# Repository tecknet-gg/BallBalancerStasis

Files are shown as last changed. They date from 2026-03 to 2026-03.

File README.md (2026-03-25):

## Overview

A project where I make a cool 3RRS parallel manipulator, and throw a camera underneath and get it to balance a ball. It uses Computer Vision (CV) to locate the ball on the platform, and then the location and velocity vector will be used to calculate the pose of the platform (using Inverse Kinematics) to then push the ball back to the centre. 

I manily made this project since it seemed cool when I saw a couple of people who had made them on YouTube (https://www.youtube.com/watch?v=v4F-cGDGiEw&t=235s), and I (being masochistic), like using PID, so here we are!

The hardware for the most part is done, and the .step file can be found in the hardware folder. Firmware is still in the very early stages, and the balancing software is yet to be written.



With the custom PCB:



Here's the BOM:

| Component | Function | Quantity | Price (unit*qty) | Source |
| --- | --- | --- | --- | --- |
| Raspberry Pi Zero 2 W | Microcontroller | 1 | £14.15 | https://shop.pimoroni.com/products/raspberry-pi-zero-2-w?variant=42101934587987 |
| Pi Camera | Camera | 1 | £7 | https://www.amazon.co.uk/dp/B0BZVP3SQW |
| Pi Zero Accessories | Assorted Accessories | 1 | £8 | https://shop.pimoroni.com/products/zero-adaptor-kit?variant=10462230279 & https://shop.pimoroni.com/products/camera-cable-raspberry-pi-zero-edition?variant=32092803891283 |
| Tie Rod | Joint | 10 | £6.99 | https://www.amazon.co.uk/dp/B0DCNGSK9S/?coliid=IMXWIUSGWOUHA&colid=3NYE67N1E05KC&psc=1 |
| M3/M4 Assortment | Strcutural | ~ | £6.64 | https://amzn.eu/d/07FYMvyj |
| DS3218MG | Servos | 3 | £29.99 | https://www.amazon.co.uk/dp/B0CY2FVZZM/?coliid=I2RXC2YMY9KN9T&colid=3NYE67N1E05KC&th=1 |
| PCA9685 | Servo Driver | 1 | £4.99 | https://www.amazon.co.uk/dp/B0BKZC1XWR/?coliid=I37WT66U57CC7J&colid=3NYE67N1E05KC&psc=1 |
| Power Supply | Power | 1 | £16.99 | https://tinyurl.com/2cr9nb7n |
| Shoulder Bolts | Pin Joints | | £4.99 | https://www.amazon.co.uk/dp/B0FDQB24SP?ref=ppx_yo2ov_dt_b_fed_asin_title |
| PLA | Printing Material | 1 | £13.99 | https://www.amazon.co.uk/dp/B0CD79M1NV?ref=ppx_yo2ov_dt_b_fed_asin_title |
| 20mm Acrylic Disc | Platform Disc | 1 | £3.49 | https://www.amazon.co.uk/dp/B0DJVB82TY/?coliid=I2NBRJSN1CBSC1&colid=3NYE67N1E05KC&psc=1 |
| 18AWG Wire | Wire | 2 | £2.90 | https://www.amazon.co.uk/dp/B0CZRGH4CT/?coliid=I36BQ0C4MRSHG2&colid=3NYE67N1E05KC&psc=1 |
| PCB | PCB | 5 | £9 | JLCPCB |

## Assembly 

You'll want to print out the files under the hardware/compoents directory in the quantities given below:

| Component | Quantity |
| --- | --- |
| feet | 6 |
| standoffs | 6 |
| baseplate | 1 |
| shield | 1 |
| bottomarm | 3 |
| toparm | 3 |
| mount | 3 |
| mountclip | 3 |

With that we start with the base and the feet. For my build, I will add some hotglue to the bottom of the each feet (the side with the smaller radius), to act as a grip. With that, its just a matter of attaching them around the circumference of the base plate. Take care to not atttach them to the holes meant for the standoffs. Use M3x6 or M3x8 screws. They are part of the screw assortment kit in the BOM if you do decide to buy the same. Reference the image below to attach the feet to the correct points.

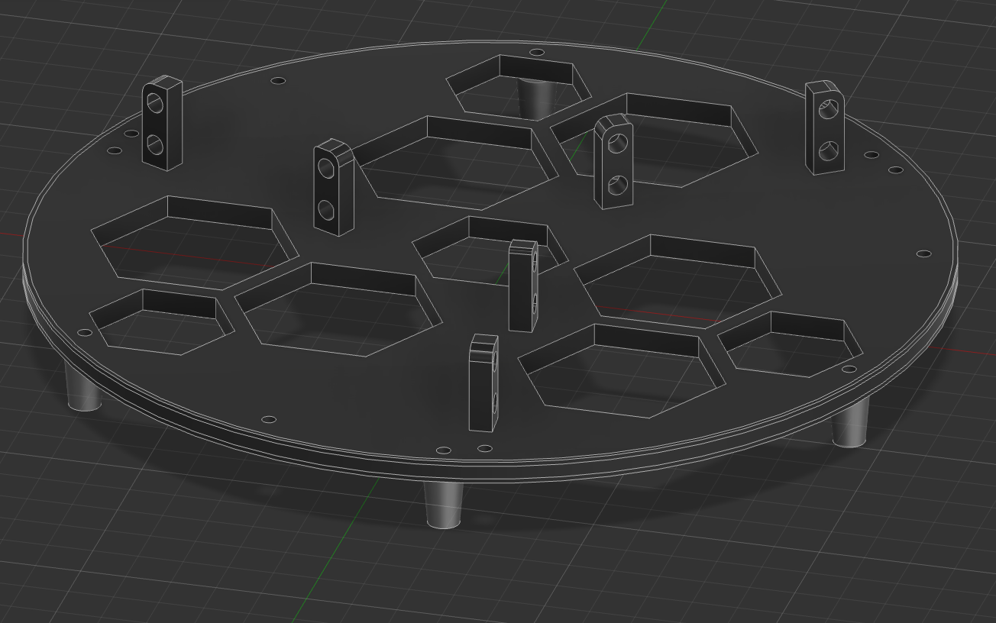
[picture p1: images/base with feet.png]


With the feet in, you'll want to grab your three servos and place them on the mounts as such:



Attach them using M3x10 bolt with a nut on the other end to clamp it in place. Also ensure you have attached the servo horn using the hardware given in the kit. Alternatively you can use an M3x6 bolt to attach the horn to the servo.

Then grab your six standoffs. Follow the same steps you did for the feet (except the hot glue grip), and attach them around the circumference using M3x8 bolts.



Now with your three bottom arms, line up the two holes on the bottom with the two on the servo horn. Using an M3x6 bolt, attach that too to the horn. You won't need a nut since the servo horn is threaded. 



Grab the three top arms now, and attach them to the bottom arms using the M4 shoulder bolt. If you want you can use a standard M4, but I use a tie rod for my build. Secure it on the other side using a lock-nut. Alternatively you could use two nuts twisted toghther tightly with some pliers.



Get your tie rods, and attach the to the top of each arm using an M3x6 or M3x8 Bolt.



You can now attach the electronics shield part to the standoffs. Just use the same M3x8 bolts and attach the shield to the six standoffs.



For the next part, my assembly doesn't have the correct compoenent in it since I don't want to redo it since I'm pretty sure I would screw up the joints, and I really don't want to do that again, so read carefully!

The mount you printed should look something like this:



You'll want to grab the M3x20mm bolt, and put it through one of the holes, then attach a nut. Proceed to screw the bolt in, and thread it through one of the tie rods. When it is on the other side of the tie rod, you'll want to add another nut. Then thread it through the other hole of the mount, and out the other end. At this side, you can use another lock nut to attach it securely. Repeat this for the three mounts. Ensure that the extended bit is pointing inwards and not outwards.

Ok now we can start assembling the electronics. Place the Pi Zero 2 W on the corresponding standoffs, and do the same with the PCA9685. No bolts required. Then place the camera module in its little enclosure. Use the attach the CSI cable to the camera, and the other end to the interface on the Pi Zero 2 (note: you'll probably need another cable specifically for the Pi Zero, one with a thinner end for the Pi Zero's CSI slot, as the stock cable with the camera is intended for the full size Pis). With the three main compoenents in, you can start wiring up the PCA9685 using this diagram (in the hardware directory):

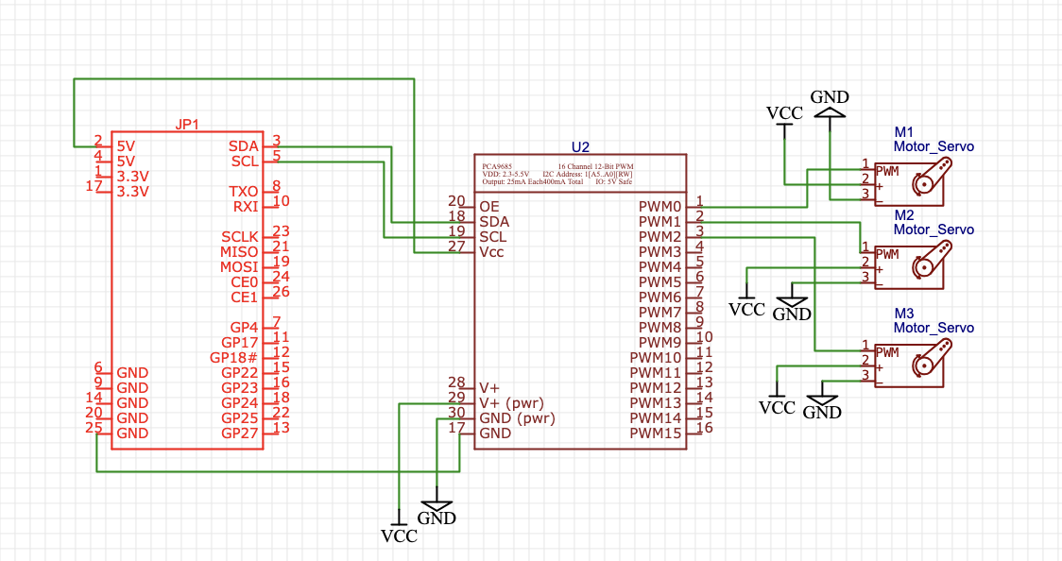
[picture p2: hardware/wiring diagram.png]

You can then attach the three servos to channels 0, 1 and 2 like in the diagram.

Finally for power, get a barrel jack to screw terminal mount, and just hot glue it somewhere onto the bottom. There's not really any mounting pounts on the screw terminal, so and I didn't really want to model in a recess specifically for that. Attach the two 18AWG wires to the screw terminals, and route it up to the PCA9685, and screw the wires into the corresponding screw terminals on the PCA9685. 

And now we can get onto mounting the platform. Grab your clear acrylic disc and the three mount clip parts. Its not on the 3D assembly, but you'll want first put some M3x6 screws through the main mount, then place the platoform in the recess, and get thread the mount clip onto the bolts, then tighten the screws. You shouldn't need a nut here, but if you end up using a longer bolt, you can. Though the piece is threaded so you shouldn't need to.



If you want to add the IMU mount like I will, you can print out the IMU Mount v4 file (x2), and just attach the IMU (MPU6050) to it, and attach it to the platoform as you did mounting the platform to the the top arm mount!



If you happen to be using the PCB, get yourself the board, solder on the DC Barrel Jack, the Pi Zero 2 W and the PCA9685. Then print out the PCB shield instead of the other shield, and mount the PCB on, and voila. Wire up the camera the same. You can wire the IMU into the I2C extender of the PCA9685 in both cases of using the PCB and not.

The PCB looks like so if you do decide to get it fabricated:



For assembling this, just desolder the headers from a Pi Zero 2 W, and put them on the underside, and solder that to the PCB. With the PCA9685, just desolder the headers too, and replace with vertical headers and again solder to the board, and you can place it on the corresponding shield! Also add 3mm LEDs if you so wish to :]

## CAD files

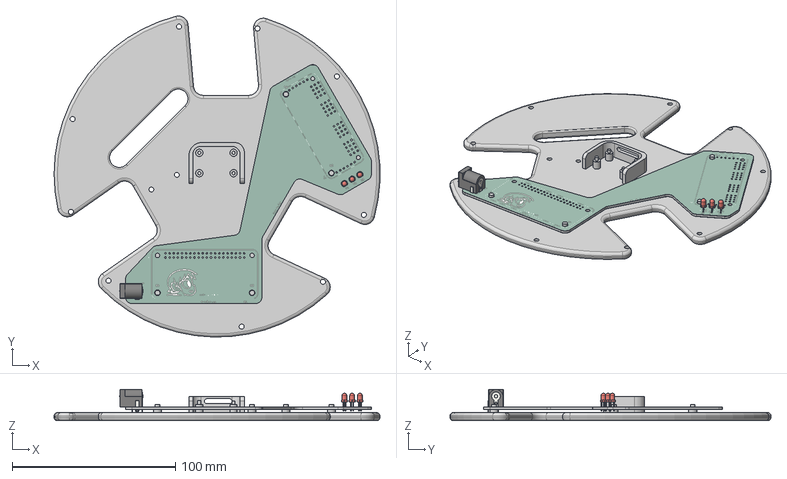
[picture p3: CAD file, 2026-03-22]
hardware/components/shieldpcb.step
199.9 x 196.9 x 19.3 mm
BarrelJack_Horizontal
LED_D3.0mm x 3
Ball Balancer_silkscreen
Ball Balancer_soldermask
Ball Balancer_PCB

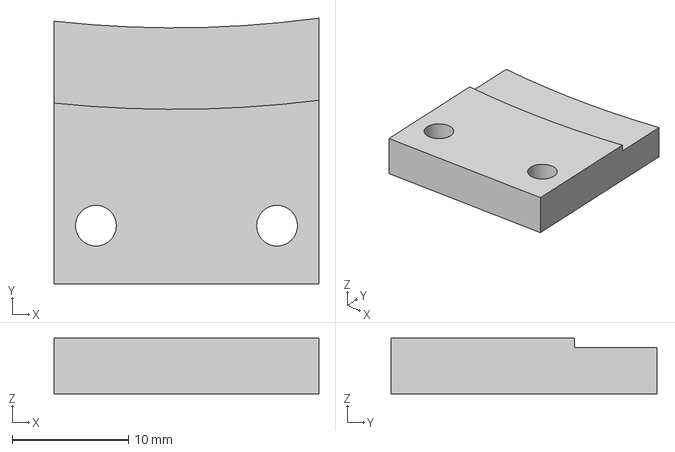
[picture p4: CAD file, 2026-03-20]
hardware/components/IMU mount v4.step
22.8 x 22.8 x 4.80 mm

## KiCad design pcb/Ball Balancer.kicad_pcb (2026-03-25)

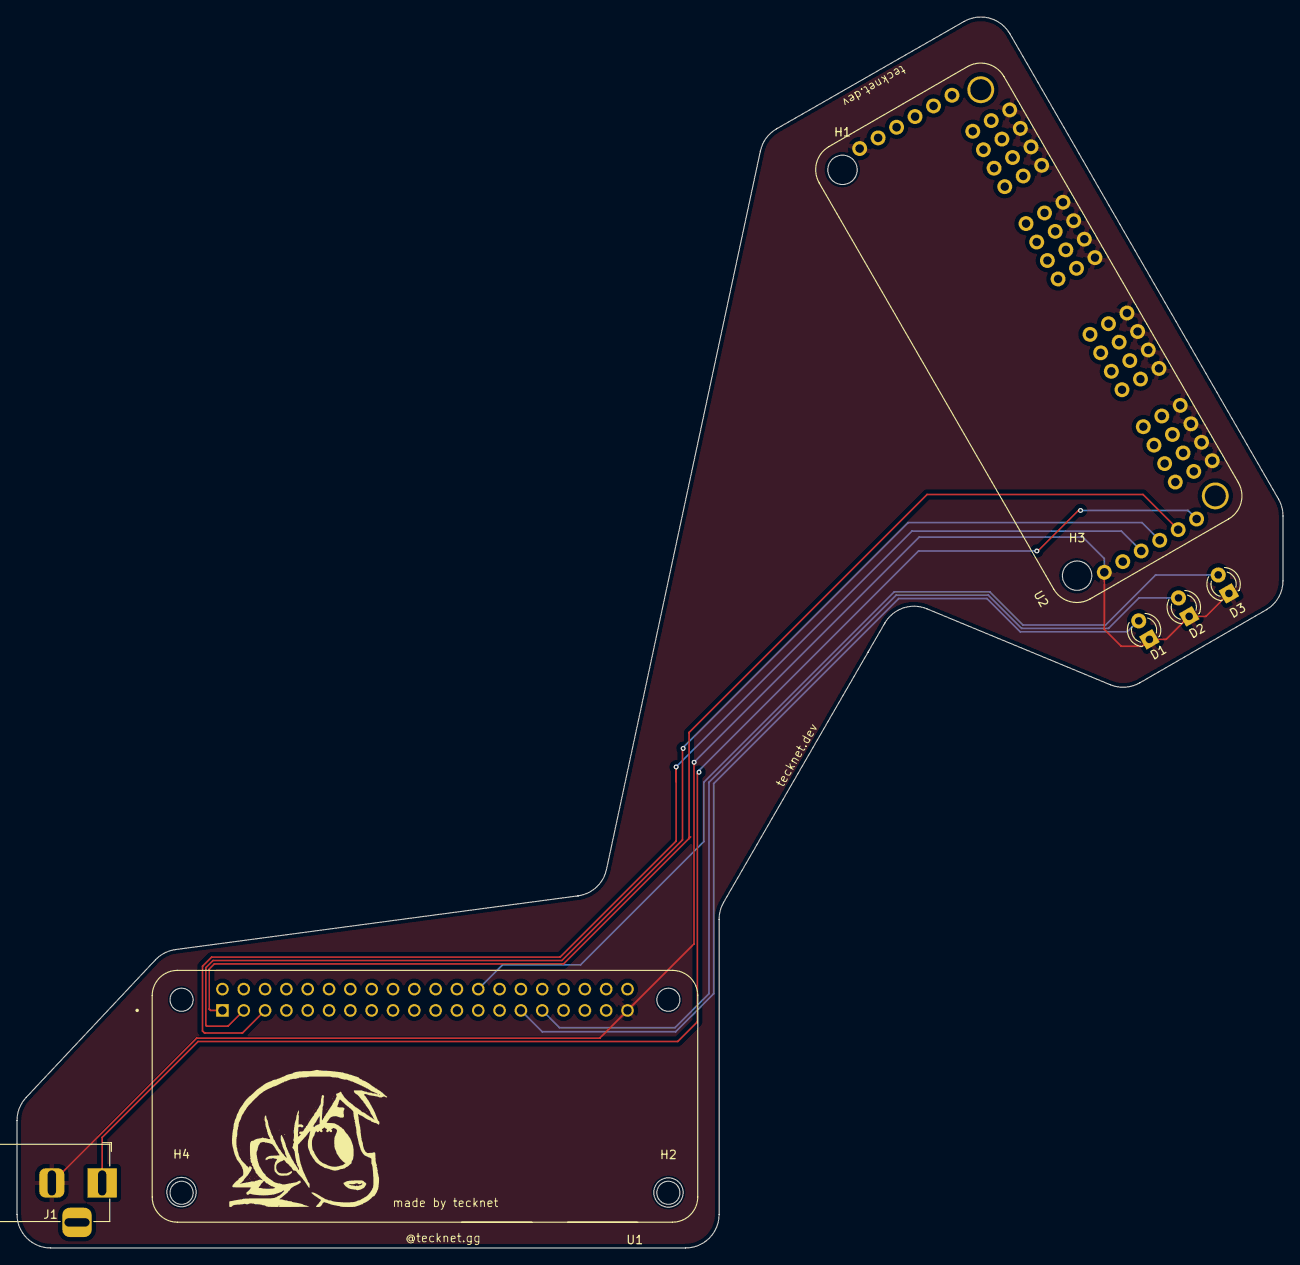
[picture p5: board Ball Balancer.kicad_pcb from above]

Board: 2 copper layers, 150.8 x 146.7 mm, 10 parts (0 on the bottom side), 9 nets.

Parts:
D1, D2, D3: LED; LED_D3.0mm
H1, H2, H3, H4: MountingHole; MountingHole_3.5mm
J1: Barrel_Jack_MountingPin; BarrelJack_Horizontal
U1: RASPBERRY_PI_ZERO_2_W; MODULE_RASPBERRY_PI_ZERO_2_W
U2: 815; MODULE_815

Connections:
GND: D1.1 (K), D2.1 (K), D3.1 (K), J1.2, U1.39 (GND_39), U2.GND_1 (GND), U2.GND_2 (GND), U2.GND_3 (GND), U2.GND_4 (GND), U2.GND_5 (GND), U2.GND_6 (GND), U2.GND_7 (GND), U2.GND_8 (GND), U2.GND_9 (GND), U2.GND_10 (GND), U2.GND_11 (GND), U2.GND_12 (GND), U2.GND_13 (GND), U2.GND_14 (GND), U2.GND_15 (GND), U2.GND_16 (GND), U2.GND_17 (GND), U2.GND_18 (GND)
unnamed: D1.2 (A), U1.29 (GPIO5)
unnamed: D2.2 (A), U1.31 (GPIO6)
unnamed: D3.2 (A), U1.26 (GPIO7/SPI_~CE1)
unnamed: U1.3 (GPIO2/SDA1), U2.SDA_1 (SDA), U2.SDA_2 (SDA)
unnamed: U1.5 (GPIO3/SCL), U2.SCL_1 (SCL), U2.SCL_2 (SCL)
unnamed: U2.OE_1 (~OE), U2.OE_2 (~OE)
V+: J1.1, U2.V+_1 (V+), U2.V+_2 (V+), U2.V+_3 (V+), U2.V+_4 (V+), U2.V+_5 (V+), U2.V+_6 (V+), U2.V+_7 (V+), U2.V+_8 (V+), U2.V+_9 (V+), U2.V+_10 (V+), U2.V+_11 (V+), U2.V+_12 (V+), U2.V+_13 (V+), U2.V+_14 (V+), U2.V+_15 (V+), U2.V+_16 (V+), U2.V+_17 (V+), U2.V+_18 (V+)
VCC: U1.1 (3V3_1), U2.VCC_1 (VCC), U2.VCC_2 (VCC)

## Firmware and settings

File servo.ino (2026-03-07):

#include <Wire.h>
#include <Adafruit_PWMServoDriver.h>

Adafruit_PWMServoDriver pwm = Adafruit_PWMServoDriver(0x40);

const int SERVO_FREQ = 50; // hz
const float MIN_PULSE_MS = 0.5; // pulse at 0
const float MAX_PULSE_MS = 2.5; // pulse at 270
const float MAX_ANGLE = 270.0; // degrees
const float PERIOD_MS = 1000.0 / SERVO_FREQ; // 20 ms
  
const float rangeMaxAngle = 60.0; // set upper constraint
const float rangeMinAngle = 15.0; // set lower constraint
  
float offset13 = 0.0; // offset for callibration
float offset14 = 0.0;
float offset15 = 0.0;
  

int angleToCount(float angle) {
	if (angle < 0) angle = 0; // redundant santiation
	if (angle > MAX_ANGLE) angle = MAX_ANGLE; // redundant santiation
  
	float pulse = MIN_PULSE_MS + (angle / MAX_ANGLE) * (MAX_PULSE_MS - MIN_PULSE_MS);
	int count = int((pulse / PERIOD_MS) * 4096.0);
	return count;
}
  
void setAngle(int channel, float angle) {
	if(angle < rangeMinAngle) angle = 360-angle;
	if(angle > rangeMaxAngle) angle = angle - (int(rangeMaxAngle/angle))*60;
	if(angle == 0) angle = rangeMinAngle;

	if(channel == 13) angle += offset13;
	if(channel == 14) angle += offset14;
	if(channel == 15) angle += offset15;

  
	angle = angleToCount(angle); //gets count
	pwm.setPWM(channel,0,angle); //pushes angle to servo
}

void testLoop() {
	for(int i=0; i<=10; i++) {
		for(int channel=13; channel<=15; channel++) {
			for(float angle=45; angle<=60;angle+=0.5) {
				setAngle(channel,angle);
				delay(1);
			}
			for(float angle=60; angle>=45; angle-=0.5) {
				setAngle(channel,angle);
				delay(1);
			}
			for(float angle=45; angle>=15; angle-=0.5) {
				setAngle(channel,angle);
				delay(1);
			}
			for(float angle=15; angle<=45; angle+=0.5) {
				setAngle(channel,angle);
				delay(1);
			}
			delay(10);
		}
	} 
	setAngle(13,45); #example usage
	setAngle(14,45);
	setAngle(15,45);
}
  
void setup() {

	Serial.begin(9600);
	pwm.begin();
	pwm.setPWMFreq(SERVO_FREQ);
	Serial.println("PCA9685 Servo Test - Channels 13/15");
  
	setAngle(13,45.0);
	setAngle(14,45.0);
	setAngle(15,45.0);
  
	delay(1000);
}
  

void loop() {
	testLoop();
}

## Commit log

2026-03-08 added bom
2026-03-16 added pictures to assembly
2026-03-16 added final image
    Updated image source for mount clip in README.
2026-03-20 added the IMU mount
    [IMU mount v4.step]
2026-03-20 added imu firmware
2026-03-20 added imu mount instructions
2026-03-22 added pcb shield
    [shieldpcb.step]
2026-03-25 added pcb images
    Added assembly instructions and PCB image for fabrication.
2026-03-25 added pcb files
    sorry stasis reviewers!
    [Ball Balancer.kicad_pcb]
